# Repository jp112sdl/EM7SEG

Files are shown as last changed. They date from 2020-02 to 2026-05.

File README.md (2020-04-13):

# EM7SEG
electro-mechanical 7 segment display (from dresser/wayne display)
<br/>
_example: use 4 of that nice vintage modules as a clock with a wemos d1 mini, that is getting its time from an ntp service through wifi_

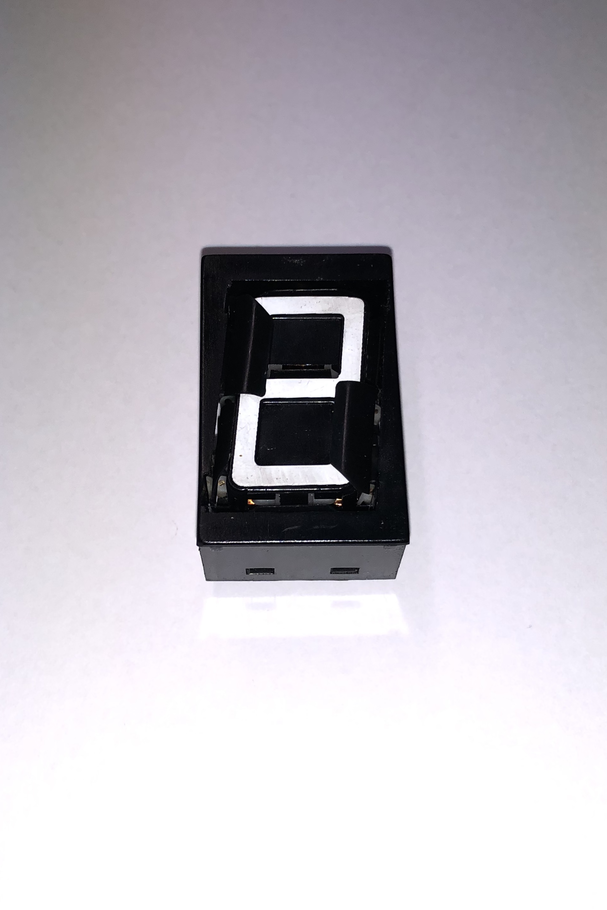
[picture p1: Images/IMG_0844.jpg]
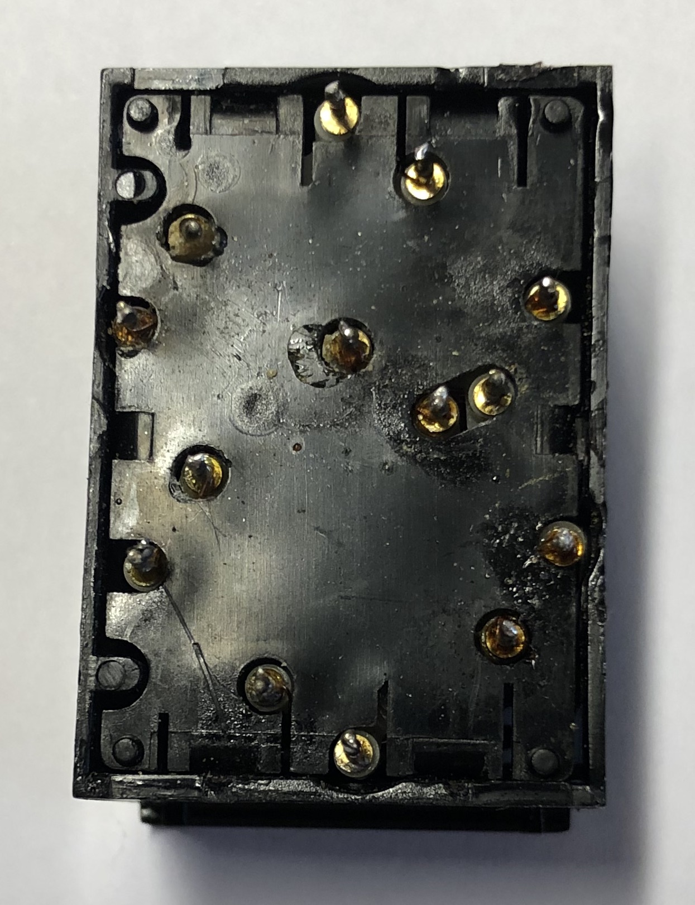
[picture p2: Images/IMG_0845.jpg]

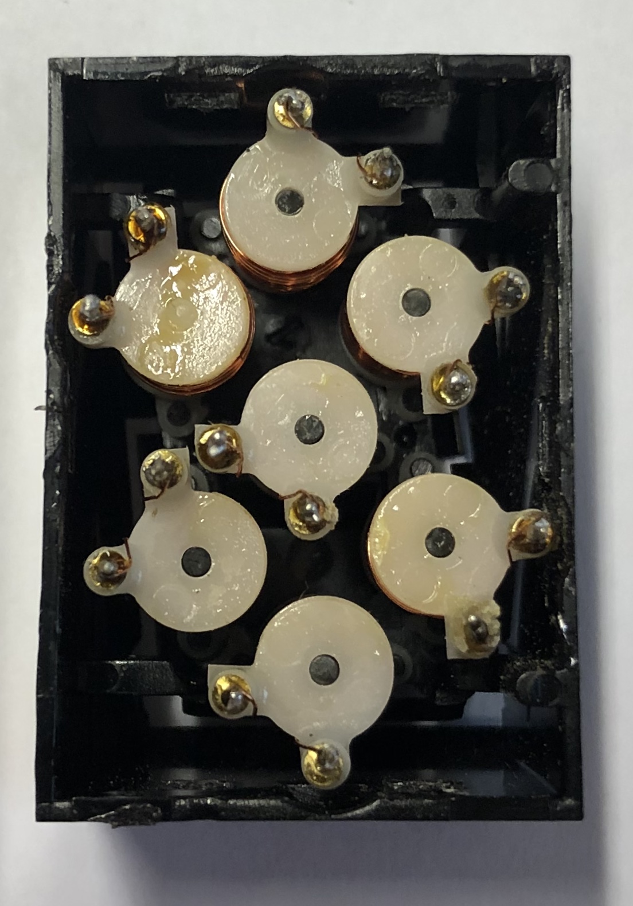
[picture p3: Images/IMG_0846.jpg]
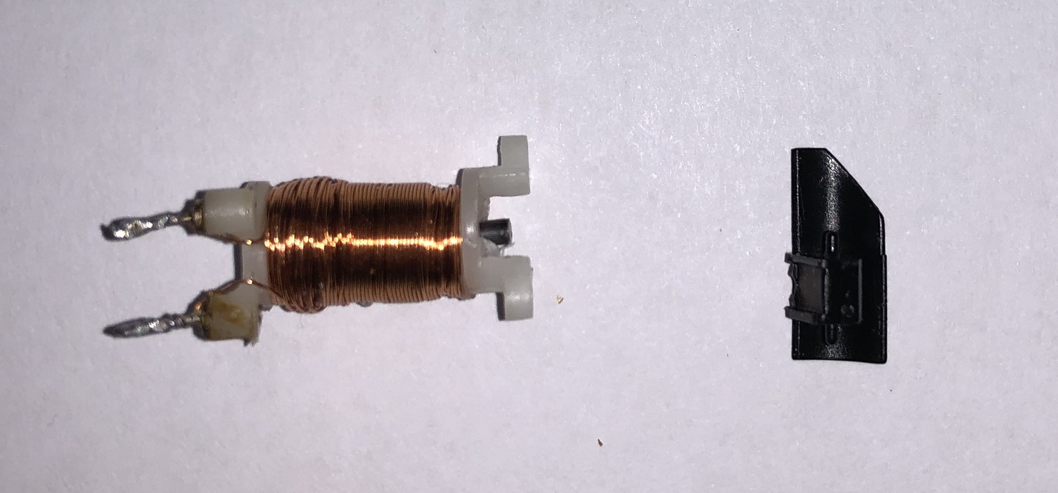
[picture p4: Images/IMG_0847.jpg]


**Teile**
| Ref | Wert | Package | JLCPCB Part |
|---|---|---|---|
| C1, C2 | 100n | 0805 | C49678 |
| R1-R4,R8-R21 | 10k | 0805 | C17414 |
| R5, R6 | 330 | 0805 | C17630 |
| R7 | 1k | 0805 | C17513 |
| D1, D2 | LED green | 0805 | C2297 |
| D3 | LED red | 0805 | C72038 |
| U2 | MCP23017-E/SS | SSOP | - |
| U3 - U9 | L9110S | TSSOP-8 | - |
| J1, J2 | Pin Header 5x | RM 2.0mm | - |

**Pin Header Zuordnung**
| Pin | Beschreibung |
|---|---|
| 1 | GND |
| 2 | Vcc Logik +3.3V / 5V|
| 3 | SDA |
| 4 | SCL |
| 5 | Vcc Segmentspulen 7.5-9V |

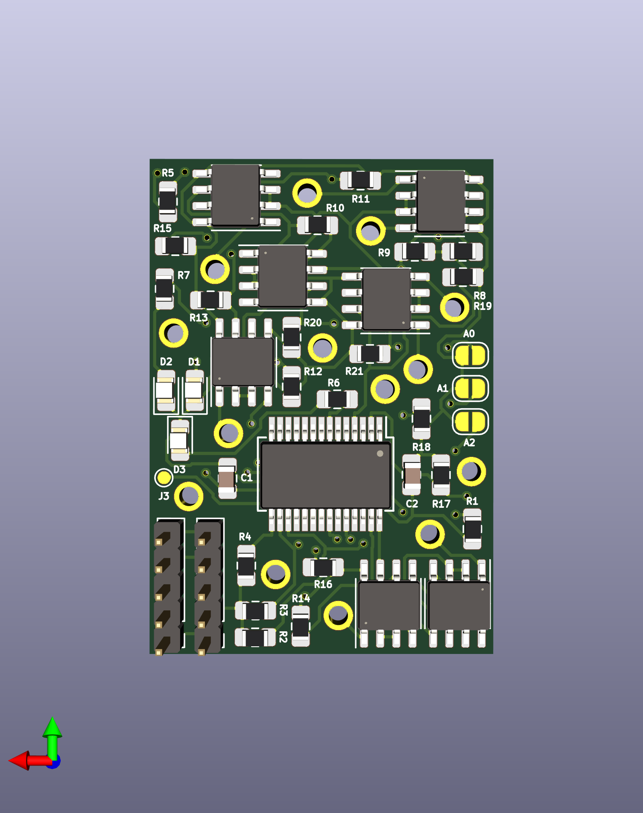
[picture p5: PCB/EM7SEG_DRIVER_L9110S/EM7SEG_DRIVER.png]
driver_pcb


## UPDATE 05.03.2020
### Die Platinen sind angekommen 😍
#### ... und ich habe vergessen, einen Motortreiber (U3) bestücken zu lassen 😤 _(aber gut, das ist kein Problem, den MCP23017 muss ich ohnehin noch selbst auflöten)_
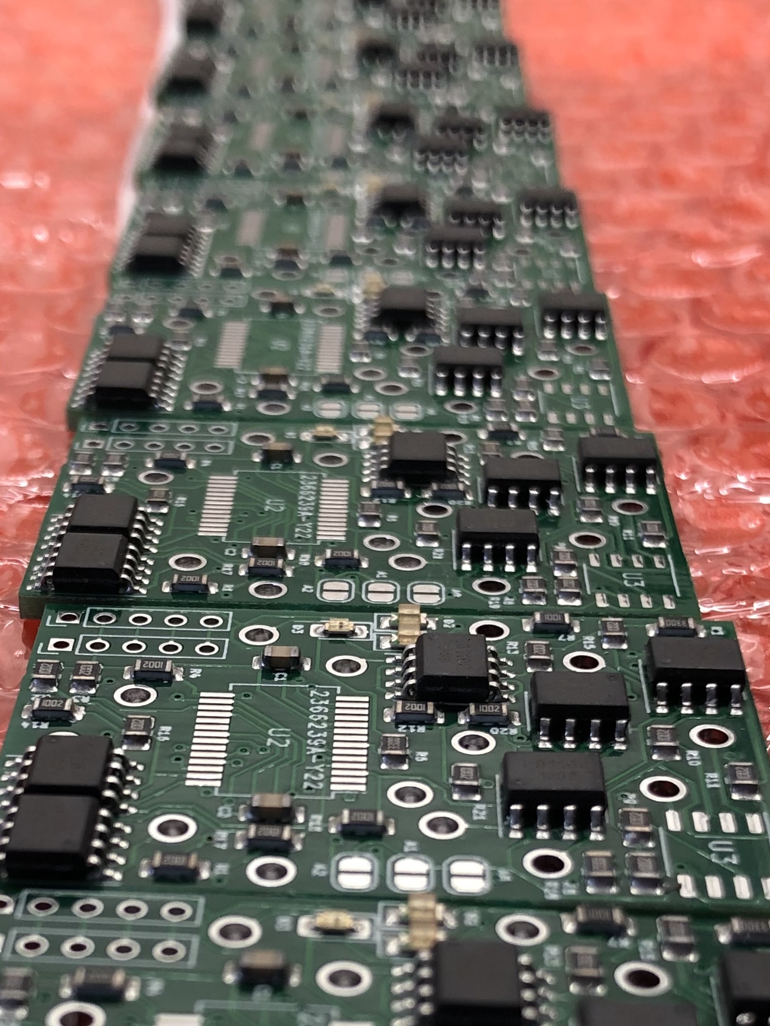
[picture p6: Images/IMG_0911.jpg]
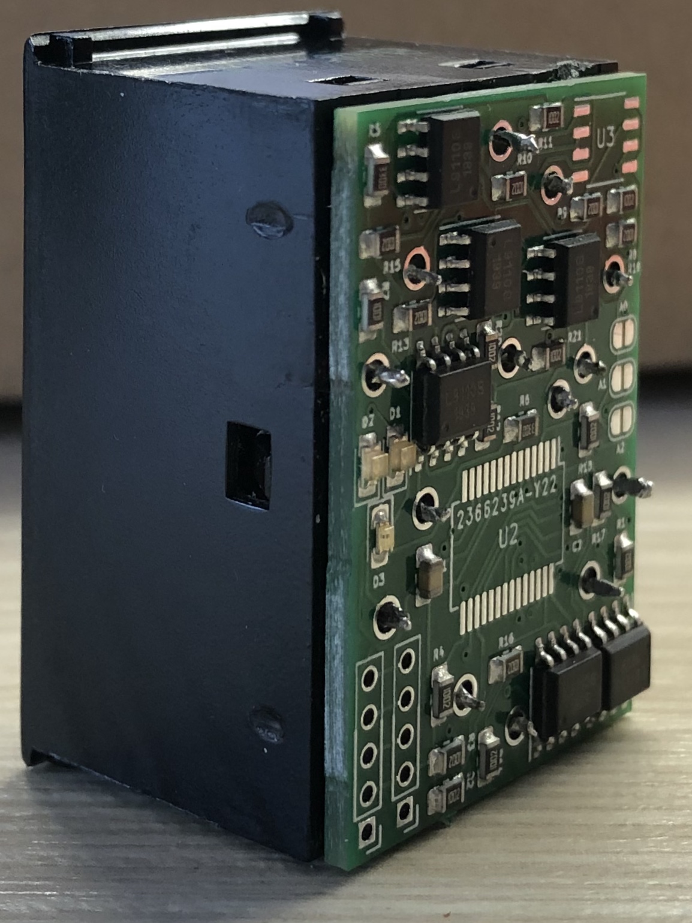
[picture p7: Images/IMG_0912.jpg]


## UPDATE 10.04.2020
### Nach einem kleinen Redesign, sind am 09.04.2020 die Platinen V2.0 gekommen,
#### ...die einen Tag später "verarbeitet wurden"
#### Am schwierigsten war der MCP23017 (SSOP) aufzulöten. Von Hand! 
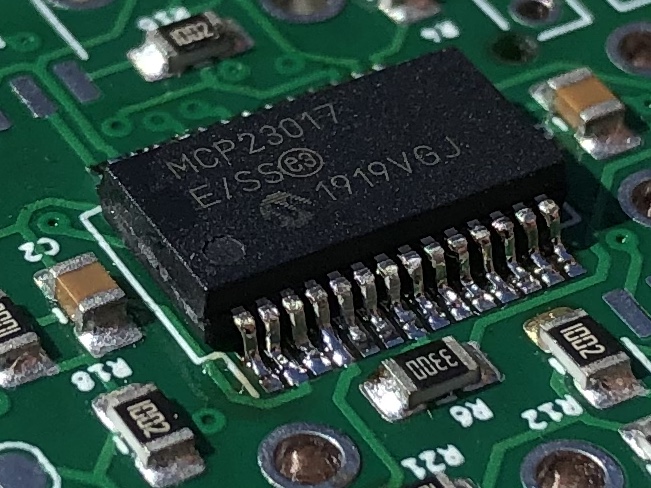
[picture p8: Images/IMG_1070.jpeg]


**Ein Mal angefangen, wurden gleich alle Platinen aufgebaut**</br>
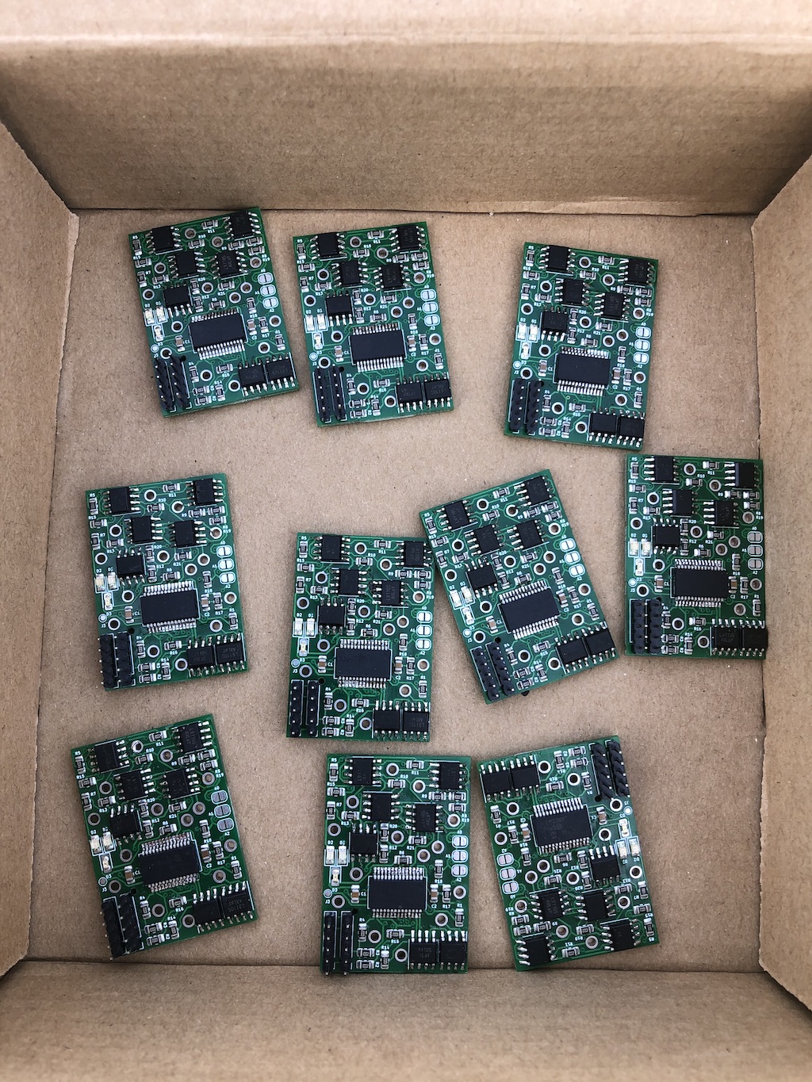
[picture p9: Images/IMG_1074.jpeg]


**und mit den Displaymodulen "verheiratet"**</br>
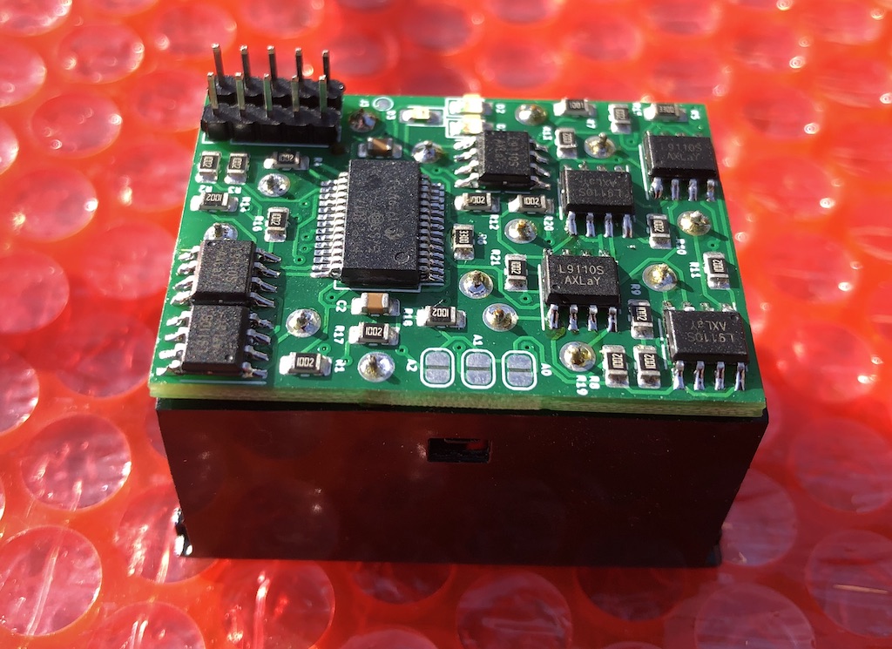
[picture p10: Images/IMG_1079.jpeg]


## UPDATE 11.04.2020
# Die Uhr läuft!
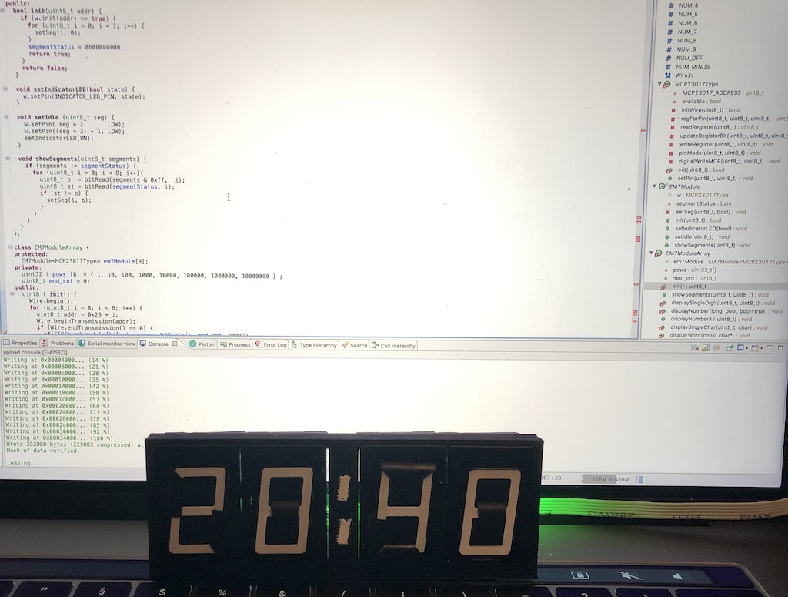
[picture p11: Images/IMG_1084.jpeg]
<br/>
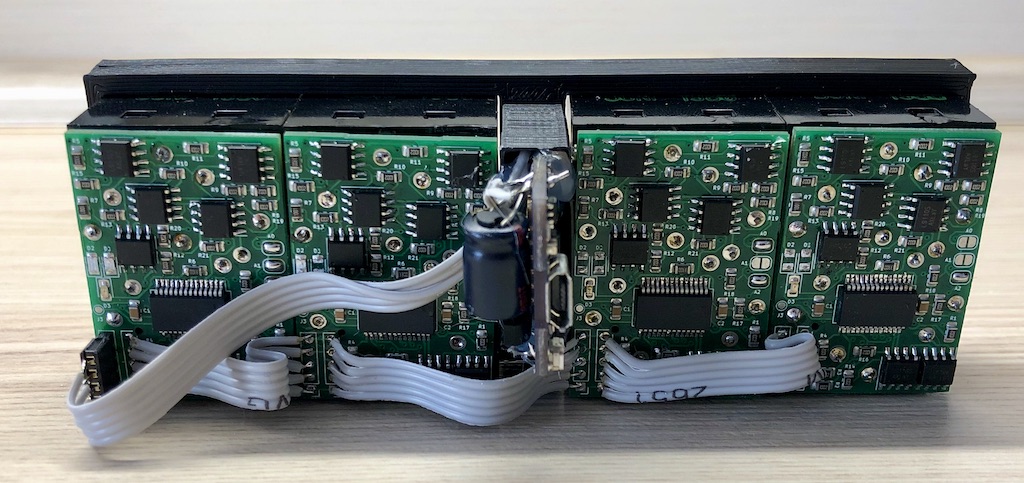
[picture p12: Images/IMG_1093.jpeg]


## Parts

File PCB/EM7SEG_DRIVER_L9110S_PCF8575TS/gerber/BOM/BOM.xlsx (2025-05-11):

Comment | Designator | Footprint | LCSC Part #（optional）
100nF | C1, C2 | 0805_C | C49678
10k | R1, R2, R3, R4,R8, R9, R10, R11, R12, R13, R14, R15, R16, R17, R18, R19, R20, R21 | 0805_R | C17414
330 | R5, R6 | 0805_R | C17630
1k | R7 | 0805_R | C17513
PCF8575TS | U2 | SSOP-24
L9110S | U3, U4, U5, U6, U7, U8, U9 | TSSOP-8
LED | D1, D2 | 0805 | C2297
LED | D3 | 0805 | C72038

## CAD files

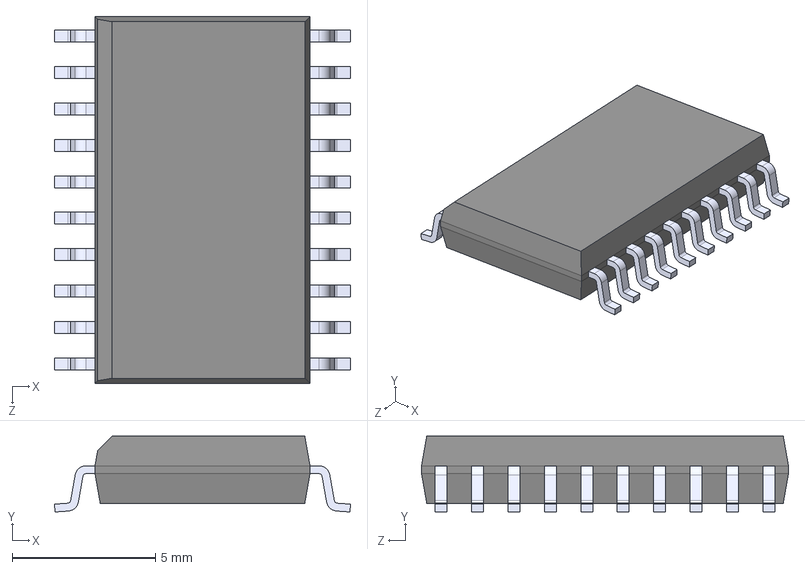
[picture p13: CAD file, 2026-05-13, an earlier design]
PCB/FP7SEG_DRIVER_DRV8848_PCF8575TS Kopie/additional/L293DD.step
10.3 x 2.65 x 12.8 mm

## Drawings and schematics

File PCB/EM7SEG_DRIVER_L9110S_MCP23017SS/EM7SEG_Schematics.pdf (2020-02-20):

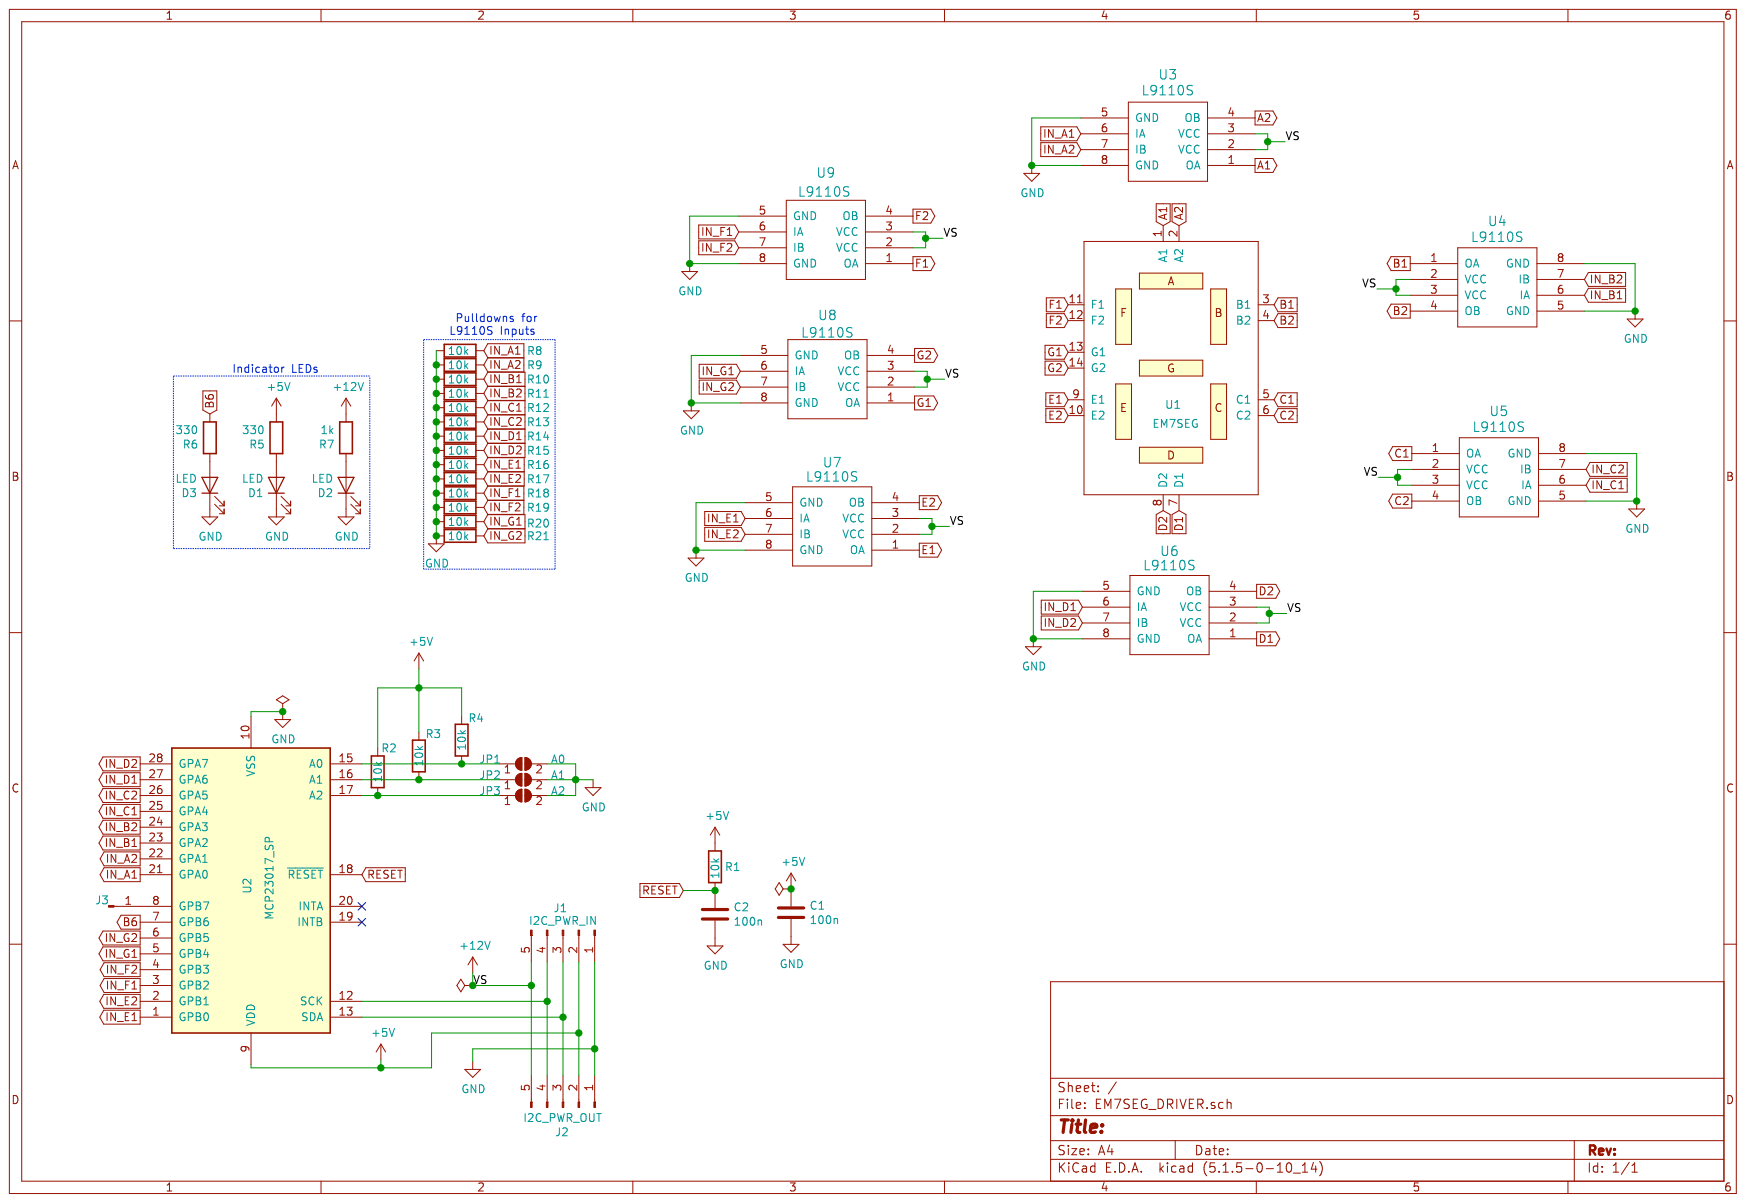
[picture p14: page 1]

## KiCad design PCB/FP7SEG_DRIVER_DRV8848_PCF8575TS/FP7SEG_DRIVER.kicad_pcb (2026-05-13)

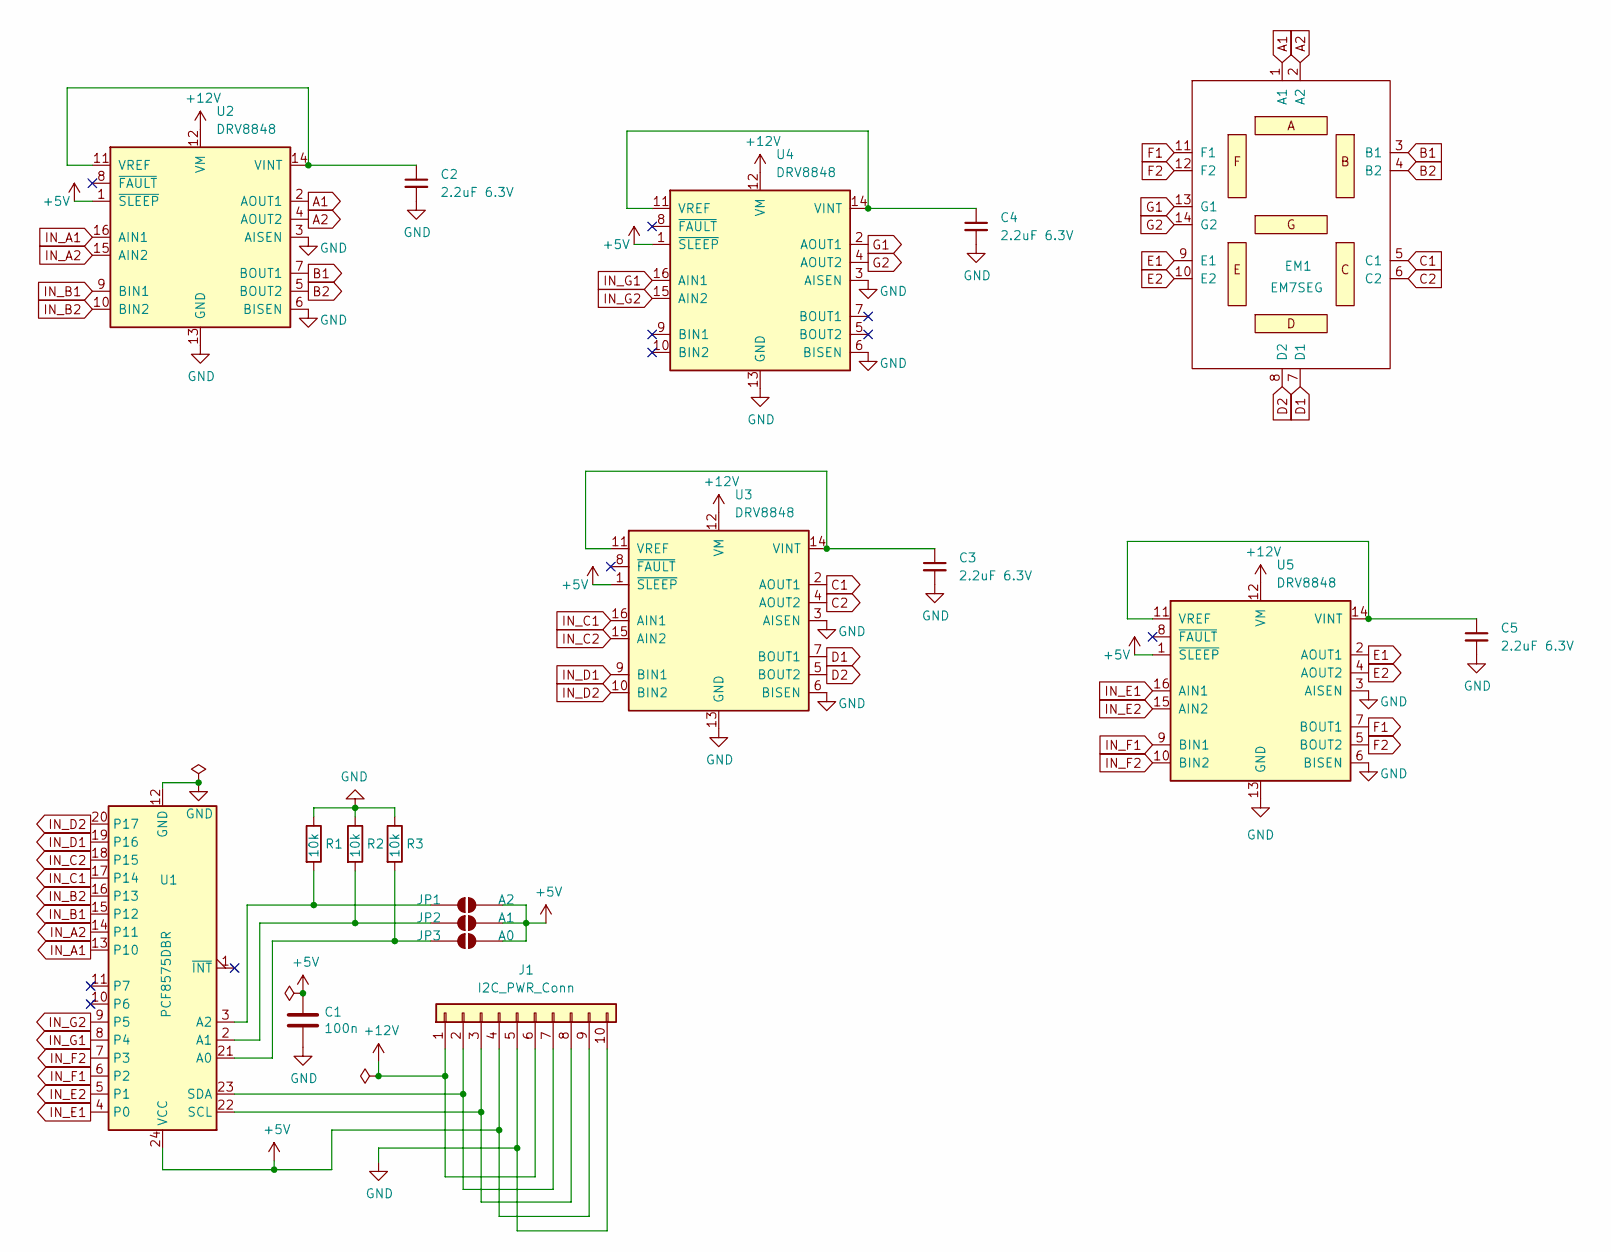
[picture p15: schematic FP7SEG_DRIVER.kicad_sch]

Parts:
C1: 100n; C_0805_2012Metric
C2, C3, C4, C5: 2.2uF 6.3V; C_0805_2012Metric
EM1: EM7SEG; FP
J1: I2C_PWR_Conn; PinSocket_1x10_P2.54mm_Vertical
JP1: A2; SolderJumper-2_P1.3mm_Open_RoundedPad1.0x1.5mm
JP2: A1; SolderJumper-2_P1.3mm_Open_RoundedPad1.0x1.5mm
JP3: A0; SolderJumper-2_P1.3mm_Open_RoundedPad1.0x1.5mm
R1, R2, R3: 10k; R_0805_2012Metric
U1: PCF8575DBR; SSOP-24_5.3x8.2mm_P0.65mm
U2, U3, U4, U5: DRV8848; TSSOP-16-1EP_4.4x5mm_P0.65mm

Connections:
+5V: C1.1, J1.4, J1.9, JP1.2 (B), JP2.2 (B), JP3.2 (B), U1.24 (VCC), U2.1 (~SLEEP), U3.1 (~SLEEP), U4.1 (~SLEEP), U5.1 (~SLEEP)
+12V: J1.1, J1.6, U2.12 (VM), U3.12 (VM), U4.12 (VM), U5.12 (VM)
A1: EM1.1 (A1), U2.2 (AOUT1)
A2: EM1.2 (A2), U2.4 (AOUT2)
B1: EM1.3 (B1), U2.7 (BOUT1)
B2: EM1.4 (B2), U2.5 (BOUT2)
C1: EM1.5 (C1), U3.2 (AOUT1)
C2: EM1.6 (C2), U3.4 (AOUT2)
D1: EM1.7 (D1), U3.7 (BOUT1)
D2: EM1.8 (D2), U3.5 (BOUT2)
E1: EM1.9 (E1), U5.2 (AOUT1)
E2: EM1.10 (E2), U5.4 (AOUT2)
F1: EM1.11 (F1), U5.7 (BOUT1)
F2: EM1.12 (F2), U5.5 (BOUT2)
G1: EM1.13 (G1), U4.2 (AOUT1)
G2: EM1.14 (G2), U4.4 (AOUT2)
GND: C1.2, C2.2, C3.2, C4.2, C5.2, J1.5, J1.10, R1.1, R2.1, R3.1, U1.12 (GND), U2.3 (AISEN), U2.6 (BISEN), U2.13 (GND), U2.17 (GND), U3.3 (AISEN), U3.6 (BISEN), U3.13 (GND), U3.17 (GND), U4.3 (AISEN), U4.6 (BISEN), U4.13 (GND), U4.17 (GND), U5.3 (AISEN), U5.6 (BISEN), U5.13 (GND), U5.17 (GND)
IN_A1: U1.13 (P10), U2.16 (AIN1)
IN_A2: U1.14 (P11), U2.15 (AIN2)
IN_B1: U1.15 (P12), U2.9 (BIN1)
IN_B2: U1.16 (P13), U2.10 (BIN2)
IN_C1: U1.17 (P14), U3.16 (AIN1)
IN_C2: U1.18 (P15), U3.15 (AIN2)
IN_D1: U1.19 (P16), U3.9 (BIN1)
IN_D2: U1.20 (P17), U3.10 (BIN2)
IN_E1: U1.4 (P0), U5.16 (AIN1)
IN_E2: U1.5 (P1), U5.15 (AIN2)
IN_F1: U1.6 (P2), U5.9 (BIN1)
IN_F2: U1.7 (P3), U5.10 (BIN2)
IN_G1: U1.8 (P4), U4.16 (AIN1)
IN_G2: U1.9 (P5), U4.15 (AIN2)
unnamed: J1.2, J1.7, U1.23 (SDA)
unnamed: J1.3, J1.8, U1.22 (SCL)
unnamed: JP1.1 (A), R1.2, U1.3 (A2)
unnamed: JP2.1 (A), R2.2, U1.2 (A1)
unnamed: JP3.1 (A), R3.2, U1.21 (A0)
unnamed: C2.1, U2.11 (VREF), U2.14 (VINT)
unnamed: C3.1, U3.11 (VREF), U3.14 (VINT)
unnamed: C4.1, U4.11 (VREF), U4.14 (VINT)
unnamed: C5.1, U5.11 (VREF), U5.14 (VINT)

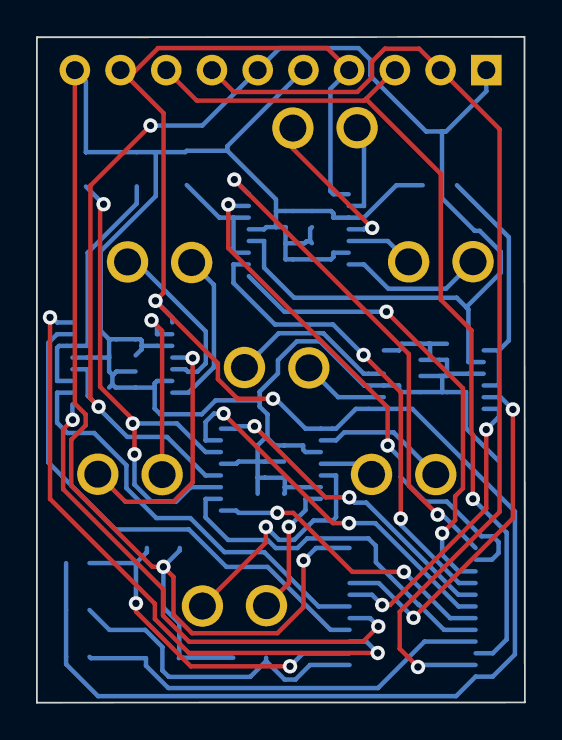
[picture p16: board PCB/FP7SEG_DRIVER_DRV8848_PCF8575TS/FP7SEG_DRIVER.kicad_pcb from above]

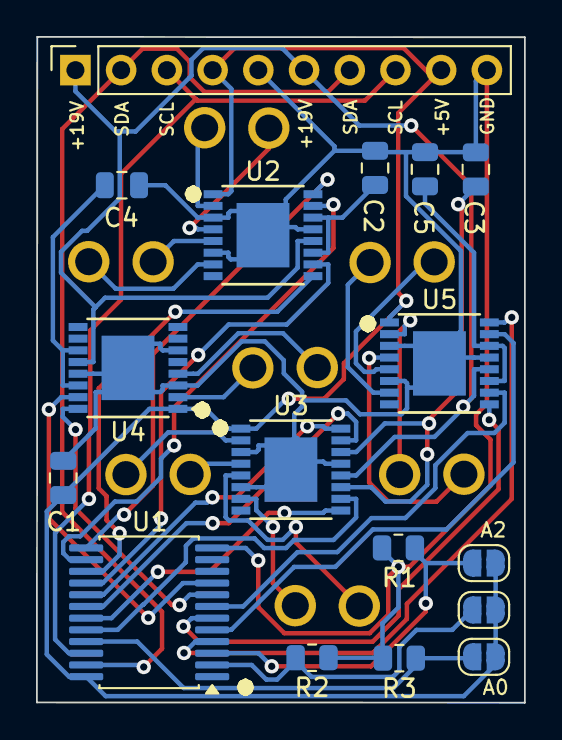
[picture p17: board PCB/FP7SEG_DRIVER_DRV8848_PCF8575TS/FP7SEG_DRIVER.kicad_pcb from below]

Board: 2 copper layers, 27.1 x 37.0 mm, 18 parts (17 on the bottom side), 40 nets.

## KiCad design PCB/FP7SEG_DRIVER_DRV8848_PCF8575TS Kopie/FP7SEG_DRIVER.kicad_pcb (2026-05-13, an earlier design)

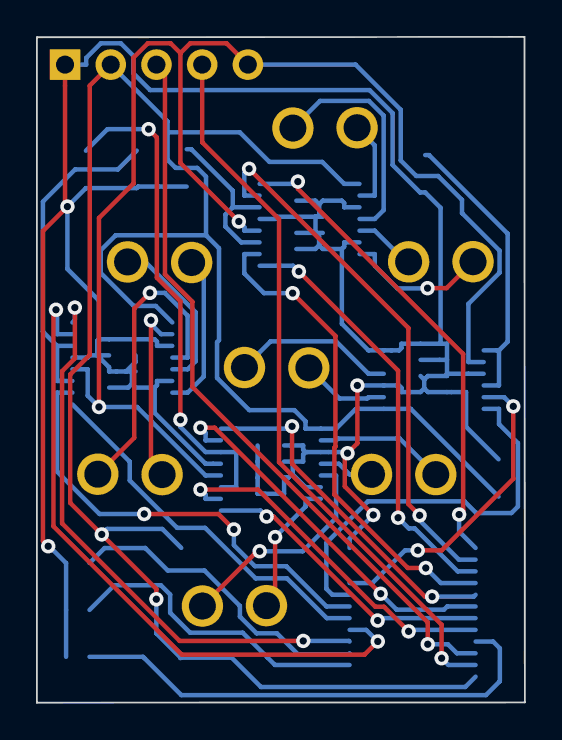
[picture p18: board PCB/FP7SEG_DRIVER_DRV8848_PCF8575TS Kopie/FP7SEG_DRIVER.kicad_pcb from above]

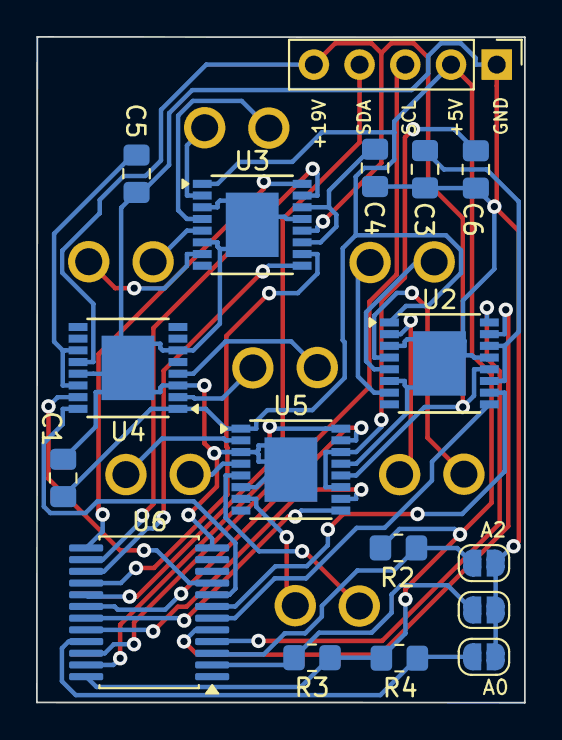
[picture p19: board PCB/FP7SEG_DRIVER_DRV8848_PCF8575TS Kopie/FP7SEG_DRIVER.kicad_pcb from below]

Board: 2 copper layers, 27.1 x 37.0 mm, 18 parts (17 on the bottom side), 40 nets.

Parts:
C1: 100n; C_0805_2012Metric_Pad1.18x1.45mm_HandSolder
C3, C4, C5, C6: 2.2uF 6.3V; C_0805_2012Metric_Pad1.18x1.45mm_HandSolder
EM1: EM7SEG; FP
J1: I2C_PWR_IN; PinHeader_1x05_P2.54mm_Vertical
JP1: A0; SolderJumper-2_P1.3mm_Open_RoundedPad1.0x1.5mm
JP2: A1; SolderJumper-2_P1.3mm_Open_RoundedPad1.0x1.5mm
JP3: A2; SolderJumper-2_P1.3mm_Open_RoundedPad1.0x1.5mm
R2, R3, R4: 10k; R_0805_2012Metric_Pad1.20x1.40mm_HandSolder
U2, U3, U4, U5: DRV8848; TSSOP-16-1EP_4.4x5mm_P0.65mm
U6: PCF8575DBR; SSOP-24_5.3x8.2mm_P0.65mm

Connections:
+5V: C1.1, J1.2, R2.1, R3.1, R4.1, U2.1 (~SLEEP), U3.1 (~SLEEP), U4.1 (~SLEEP), U5.1 (~SLEEP), U6.24 (VCC)
+12V: J1.5, U2.12 (VM), U3.12 (VM), U4.12 (VM), U5.12 (VM)
A1: EM1.1 (A1), U3.2 (AOUT1)
A2: EM1.2 (A2), U3.4 (AOUT2)
B1: EM1.3 (B1), U3.7 (BOUT1)
B2: EM1.4 (B2), U3.5 (BOUT2)
C1: EM1.5 (C1), U5.2 (AOUT1)
C2: EM1.6 (C2), U5.4 (AOUT2)
D1: EM1.7 (D1), U5.7 (BOUT1)
D2: EM1.8 (D2), U5.5 (BOUT2)
E1: EM1.9 (E1), U2.2 (AOUT1)
E2: EM1.10 (E2), U2.4 (AOUT2)
F1: EM1.11 (F1), U2.7 (BOUT1)
F2: EM1.12 (F2), U2.5 (BOUT2)
G1: EM1.13 (G1), U4.2 (AOUT1)
G2: EM1.14 (G2), U4.4 (AOUT2)
GND: C1.2, C3.2, C4.2, C5.2, C6.2, J1.1, JP1.2 (B), JP2.2 (B), JP3.2 (B), U2.3 (AISEN), U2.6 (BISEN), U2.13 (GND), U2.17 (GND), U3.3 (AISEN), U3.6 (BISEN), U3.13 (GND), U3.17 (GND), U4.3 (AISEN), U4.6 (BISEN), U4.13 (GND), U4.17 (GND), U5.3 (AISEN), U5.6 (BISEN), U5.13 (GND), U5.17 (GND), U6.12 (GND)
IN_A1: U3.16 (AIN1), U6.13 (P10)
IN_A2: U3.15 (AIN2), U6.14 (P11)
IN_B1: U3.9 (BIN1), U6.15 (P12)
IN_B2: U3.10 (BIN2), U6.16 (P13)
IN_C1: U5.16 (AIN1), U6.17 (P14)
IN_C2: U5.15 (AIN2), U6.18 (P15)
IN_D1: U5.9 (BIN1), U6.19 (P16)
IN_D2: U5.10 (BIN2), U6.20 (P17)
IN_E1: U2.16 (AIN1), U6.4 (P0)
IN_E2: U2.15 (AIN2), U6.5 (P1)
IN_F1: U2.9 (BIN1), U6.6 (P2)
IN_F2: U2.10 (BIN2), U6.7 (P3)
IN_G1: U4.16 (AIN1), U6.8 (P4)
IN_G2: U4.15 (AIN2), U6.9 (P5)
unnamed: J1.3, U6.22 (SCL)
unnamed: J1.4, U6.23 (SDA)
unnamed: JP1.1 (A), R4.2, U6.21 (A0)
unnamed: JP2.1 (A), R3.2, U6.2 (A1)
unnamed: JP3.1 (A), R2.2, U6.3 (A2)
unnamed: C3.1, U2.11 (VREF), U2.14 (VINT)
unnamed: C4.1, U3.11 (VREF), U3.14 (VINT)
unnamed: C5.1, U4.11 (VREF), U4.14 (VINT)
unnamed: C6.1, U5.11 (VREF), U5.14 (VINT)

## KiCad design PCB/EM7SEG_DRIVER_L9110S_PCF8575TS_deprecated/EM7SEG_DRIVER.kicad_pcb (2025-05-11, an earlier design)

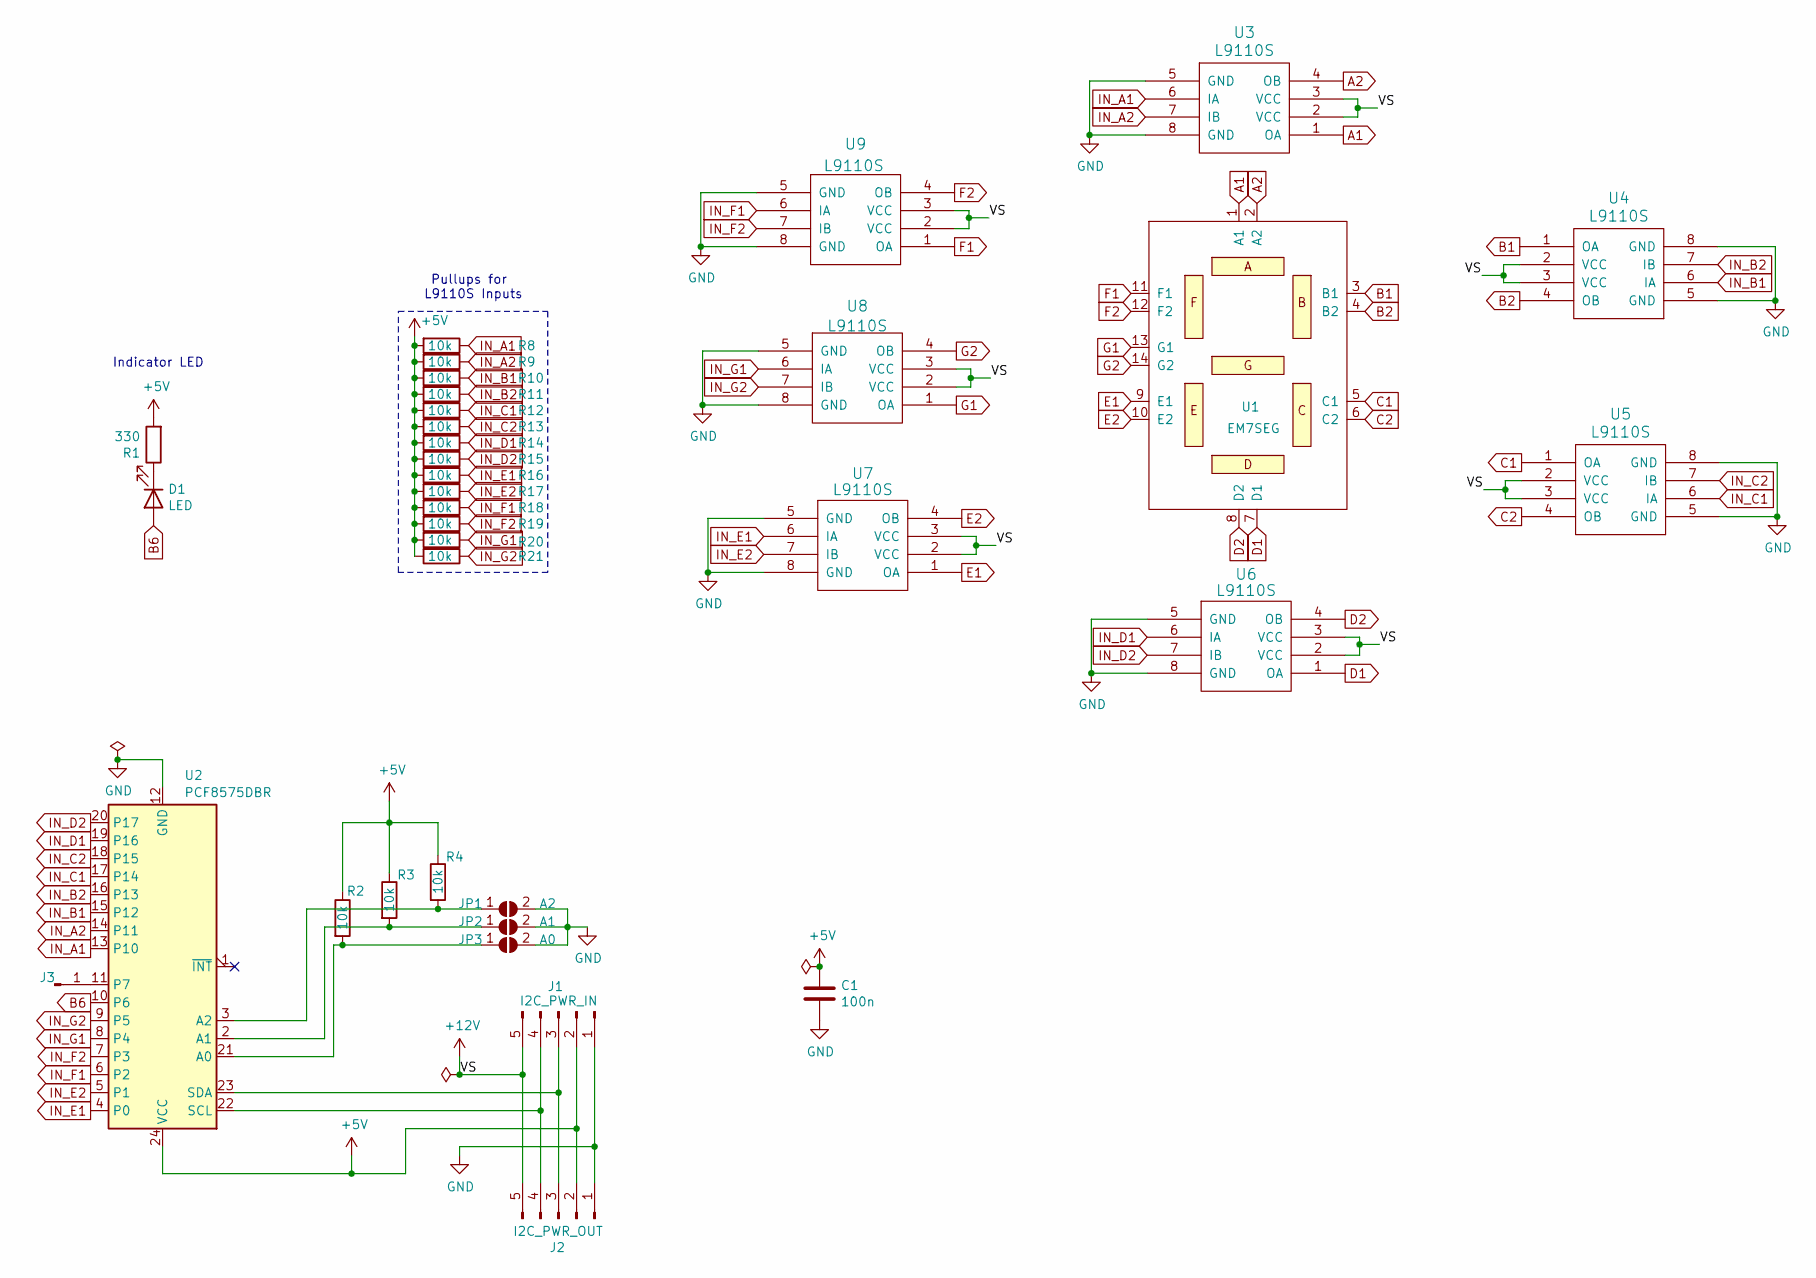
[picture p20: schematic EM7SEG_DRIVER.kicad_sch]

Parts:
C1: 100n; C_0805_2012Metric_Pad1.15x1.40mm_HandSolder
D1: LED; LED_0805_2012Metric_Pad1.15x1.40mm_HandSolder
J1: I2C_PWR_IN; PinHeader_1x05_P2.00mm_Vertical
J2: I2C_PWR_OUT; PinHeader_1x05_P2.00mm_Vertical
J3: Pad_IO16; TestPoint_Pad_D1.0mm
JP1: A0; SolderJumper-2_P1.3mm_Open_RoundedPad1.0x1.5mm
JP2: A1; SolderJumper-2_P1.3mm_Open_RoundedPad1.0x1.5mm
JP3: A2; SolderJumper-2_P1.3mm_Open_RoundedPad1.0x1.5mm
R1: 330; R_0805_2012Metric_Pad1.15x1.40mm_HandSolder
R2, R3, R4, R8, R9, R10, R11, R12, R13, R14, R15, R16, R17, R18, R19, R20, R21: 10k; R_0805_2012Metric_Pad1.15x1.40mm_HandSolder
U1: EM7SEG; em7seg
U2: PCF8575DBR; SSOP-24_5.3x8.2mm_P0.65mm
U3, U4, U5, U6, U7, U8, U9: L9110S; SOP-8_3.9x4.9mm_P1.27mm

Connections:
+5V: C1.1, J1.2, J2.2, R1.2, R2.1, R3.1, R4.1, R8.2, R9.2, R10.2, R11.2, R12.2, R13.2, R14.2, R15.2, R16.2, R17.2, R18.2, R19.2, R20.2, R21.2, U2.24 (VCC)
+12V: J1.5, J2.5, U3.2 (VCC), U3.3 (VCC), U4.2 (VCC), U4.3 (VCC), U5.2 (VCC), U5.3 (VCC), U6.2 (VCC), U6.3 (VCC), U7.2 (VCC), U7.3 (VCC), U8.2 (VCC), U8.3 (VCC), U9.2 (VCC), U9.3 (VCC)
A1: U1.1 (A1), U3.1 (OA)
A2: U1.2 (A2), U3.4 (OB)
B1: U1.3 (B1), U4.1 (OA)
B2: U1.4 (B2), U4.4 (OB)
B6: D1.2 (A), U2.10 (P6)
C1: U1.5 (C1), U5.1 (OA)
C2: U1.6 (C2), U5.4 (OB)
D1: U1.7 (D1), U6.1 (OA)
D2: U1.8 (D2), U6.4 (OB)
E1: U1.9 (E1), U7.1 (OA)
E2: U1.10 (E2), U7.4 (OB)
F1: U1.11 (F1), U9.1 (OA)
F2: U1.12 (F2), U9.4 (OB)
G1: U1.13 (G1), U8.1 (OA)
G2: U1.14 (G2), U8.4 (OB)
GND: C1.2, J1.1, J2.1, JP1.2 (B), JP2.2 (B), JP3.2 (B), U2.12 (GND), U3.5 (GND), U3.8 (GND), U4.5 (GND), U4.8 (GND), U5.5 (GND), U5.8 (GND), U6.5 (GND), U6.8 (GND), U7.5 (GND), U7.8 (GND), U8.5 (GND), U8.8 (GND), U9.5 (GND), U9.8 (GND)
IN_A1: R8.1, U2.13 (P10), U3.6 (IA)
IN_A2: R9.1, U2.14 (P11), U3.7 (IB)
IN_B1: R10.1, U2.15 (P12), U4.6 (IA)
IN_B2: R11.1, U2.16 (P13), U4.7 (IB)
IN_C1: R12.1, U2.17 (P14), U5.6 (IA)
IN_C2: R13.1, U2.18 (P15), U5.7 (IB)
IN_D1: R14.1, U2.19 (P16), U6.6 (IA)
IN_D2: R15.1, U2.20 (P17), U6.7 (IB)
IN_E1: R16.1, U2.4 (P0), U7.6 (IA)
IN_E2: R17.1, U2.5 (P1), U7.7 (IB)
IN_F1: R18.1, U2.6 (P2), U9.6 (IA)
IN_F2: R19.1, U2.7 (P3), U9.7 (IB)
IN_G1: R20.1, U2.8 (P4), U8.6 (IA)
IN_G2: R21.1, U2.9 (P5), U8.7 (IB)
unnamed: D1.1 (K), R1.1
unnamed: J1.3, J2.3, U2.23 (SDA)
unnamed: J1.4, J2.4, U2.22 (SCL)
unnamed: J3.1, U2.11 (P7)
unnamed: JP1.1 (A), R4.2, U2.3 (A2)
unnamed: JP2.1 (A), R3.2, U2.2 (A1)
unnamed: JP3.1 (A), R2.2, U2.21 (A0)

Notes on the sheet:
Pullups for L9110S Inputs
Indicator LED

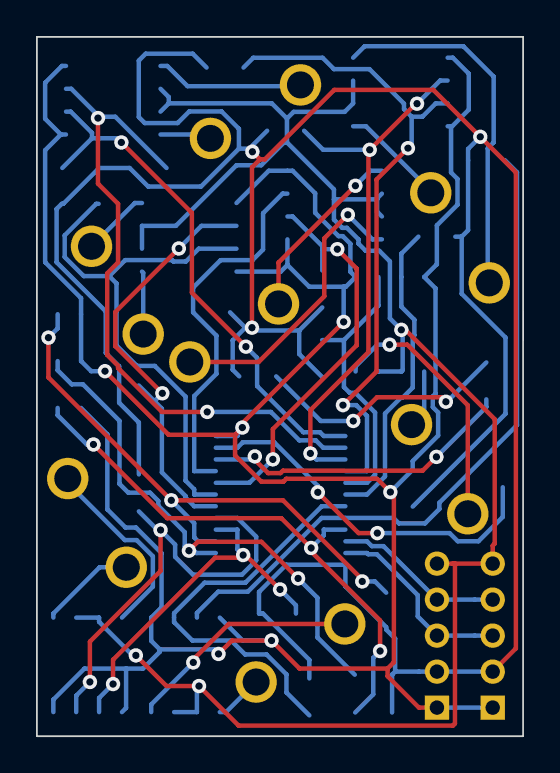
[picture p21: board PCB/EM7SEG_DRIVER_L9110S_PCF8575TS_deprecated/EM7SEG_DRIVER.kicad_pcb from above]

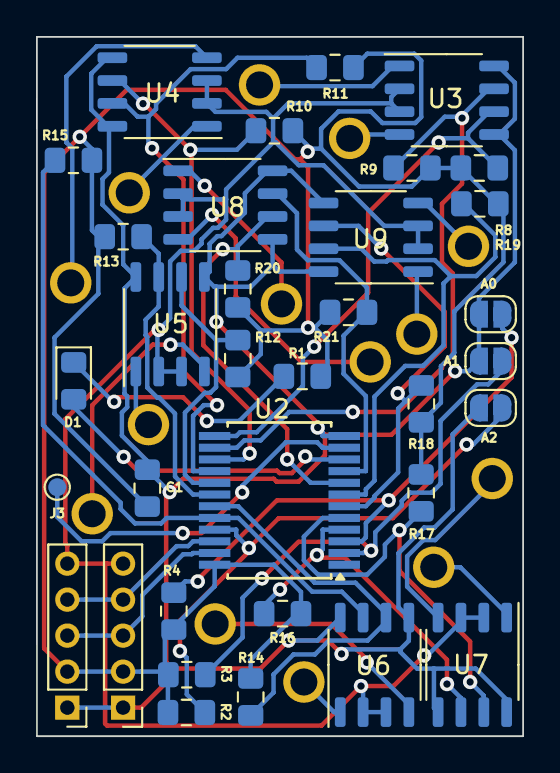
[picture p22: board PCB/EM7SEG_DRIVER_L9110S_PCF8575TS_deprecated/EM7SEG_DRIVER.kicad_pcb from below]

Board: 2 copper layers, 27.0 x 38.8 mm, 35 parts (34 on the bottom side), 39 nets.

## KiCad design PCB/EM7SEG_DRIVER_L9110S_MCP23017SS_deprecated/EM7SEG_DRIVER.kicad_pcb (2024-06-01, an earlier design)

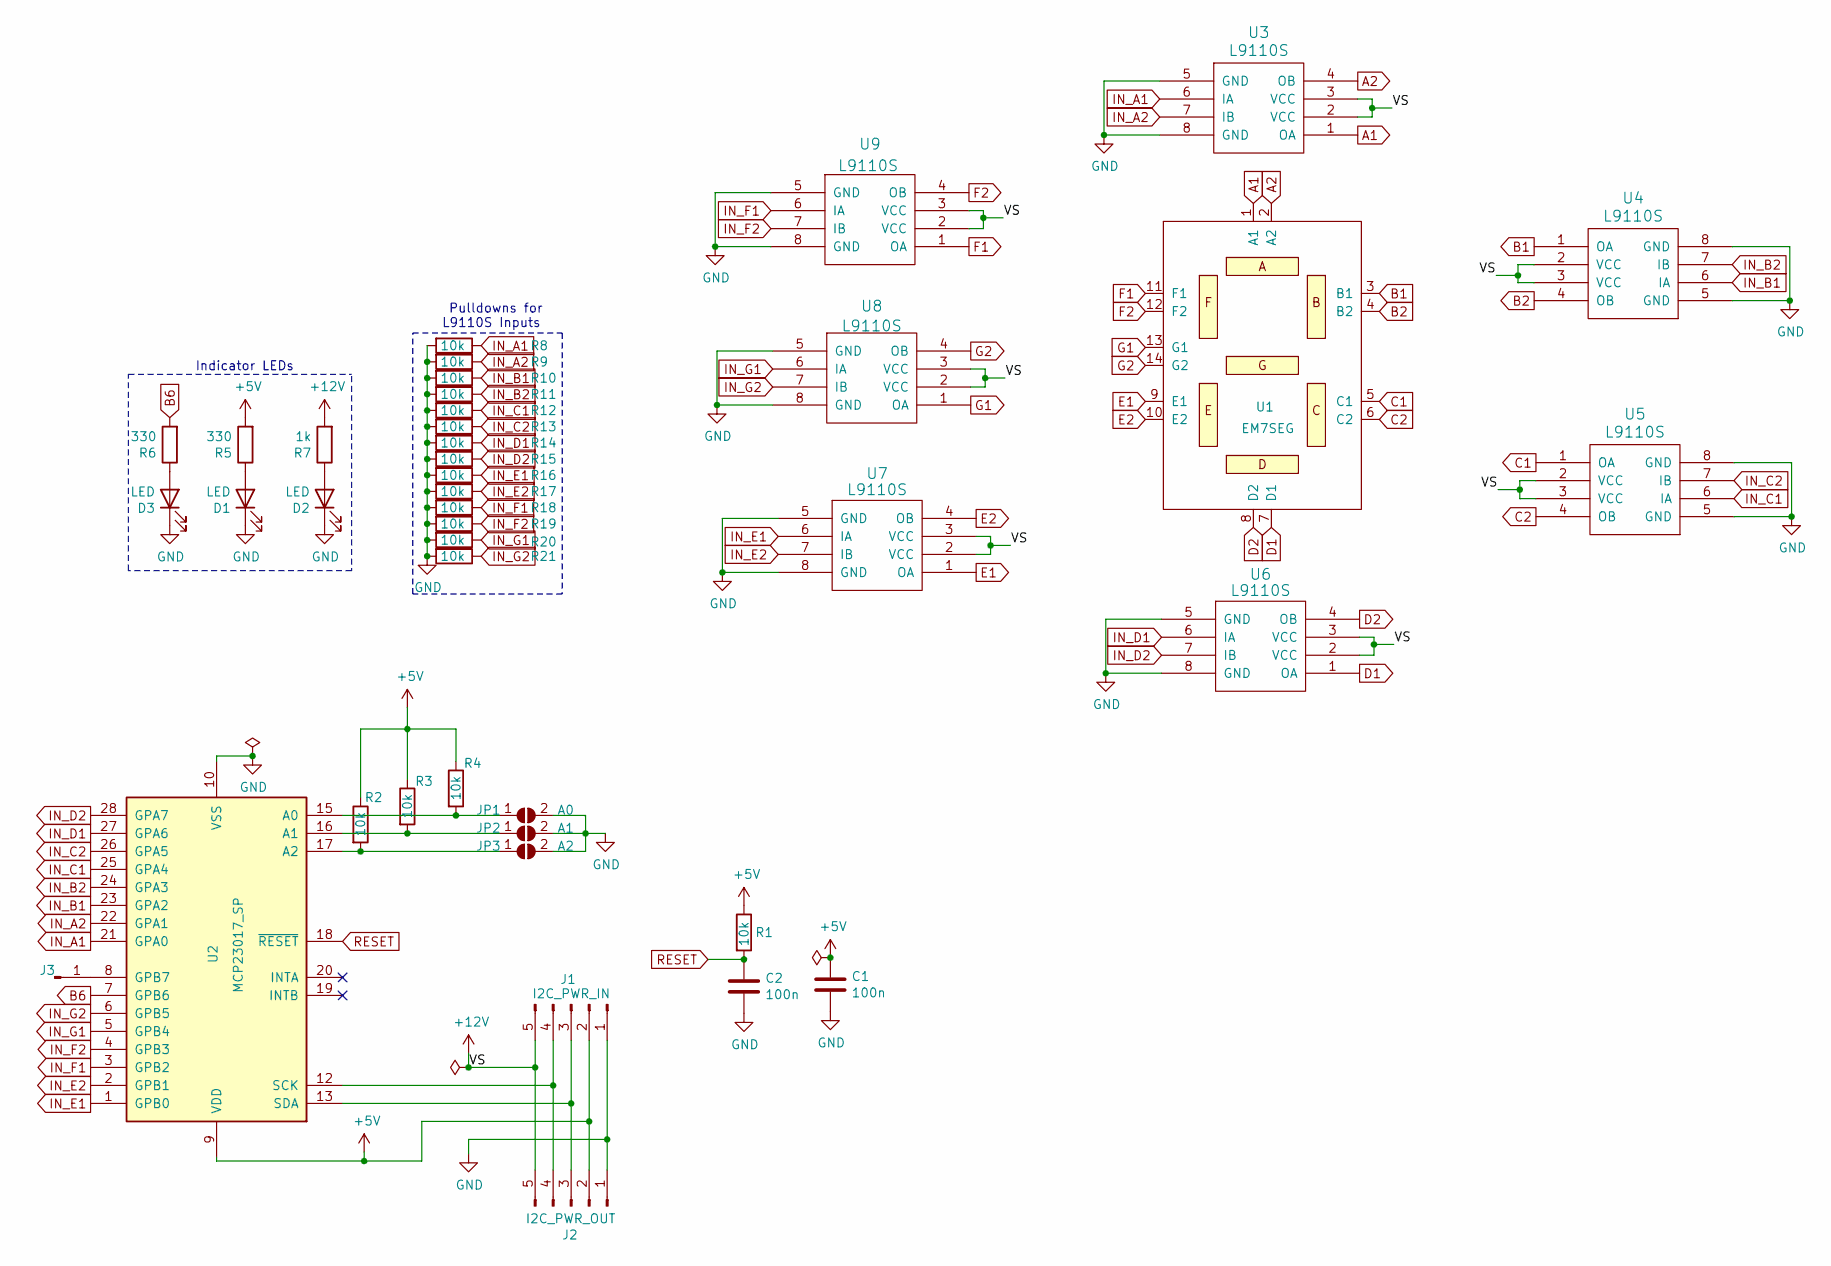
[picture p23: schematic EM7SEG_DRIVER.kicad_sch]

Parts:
C1, C2: 100n; C_0805_2012Metric_Pad1.15x1.40mm_HandSolder
D1, D2, D3: LED; LED_0805_2012Metric_Pad1.15x1.40mm_HandSolder
J1: I2C_PWR_IN; PinHeader_1x05_P2.00mm_Vertical
J2: I2C_PWR_OUT; PinHeader_1x05_P2.00mm_Vertical
J3: Pad_IO16; TestPoint_Pad_D1.0mm
JP1: A0; SolderJumper-2_P1.3mm_Open_RoundedPad1.0x1.5mm
JP2: A1; SolderJumper-2_P1.3mm_Open_RoundedPad1.0x1.5mm
JP3: A2; SolderJumper-2_P1.3mm_Open_RoundedPad1.0x1.5mm
R1, R2, R3, R4, R8, R9, R10, R11, R12, R13, R14, R15, R16, R17, R18, R19, R20, R21: 10k; R_0805_2012Metric_Pad1.15x1.40mm_HandSolder
R5, R6: 330; R_0805_2012Metric_Pad1.15x1.40mm_HandSolder
R7: 1k; R_0805_2012Metric_Pad1.15x1.40mm_HandSolder
U1: EM7SEG; em7seg
U2: MCP23017_SP; SSOP-28_5.3x10.2mm_P0.65mm
U3, U4, U5, U6, U7, U8, U9: L9110S; SOP-8_3.9x4.9mm_P1.27mm

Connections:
+5V: C1.1, J1.2, J2.2, R1.1, R2.1, R3.1, R4.1, R5.2, U2.9 (VDD)
+12V: J1.5, J2.5, R7.2, U3.2 (VCC), U3.3 (VCC), U4.2 (VCC), U4.3 (VCC), U5.2 (VCC), U5.3 (VCC), U6.2 (VCC), U6.3 (VCC), U7.2 (VCC), U7.3 (VCC), U8.2 (VCC), U8.3 (VCC), U9.2 (VCC), U9.3 (VCC)
A1: U1.1 (A1), U3.1 (OA)
A2: U1.2 (A2), U3.4 (OB)
B1: U1.3 (B1), U4.1 (OA)
B2: U1.4 (B2), U4.4 (OB)
B6: R6.2, U2.7 (GPB6)
C1: U1.5 (C1), U5.1 (OA)
C2: U1.6 (C2), U5.4 (OB)
D1: U1.7 (D1), U6.1 (OA)
D2: U1.8 (D2), U6.4 (OB)
E1: U1.9 (E1), U7.1 (OA)
E2: U1.10 (E2), U7.4 (OB)
F1: U1.11 (F1), U9.1 (OA)
F2: U1.12 (F2), U9.4 (OB)
G1: U1.13 (G1), U8.1 (OA)
G2: U1.14 (G2), U8.4 (OB)
GND: C1.2, C2.2, D1.1 (K), D2.1 (K), D3.1 (K), J1.1, J2.1, JP1.2 (B), JP2.2 (B), JP3.2 (B), R8.2, R9.2, R10.2, R11.2, R12.2, R13.2, R14.2, R15.2, R16.2, R17.2, R18.2, R19.2, R20.2, R21.2, U2.10 (VSS), U3.5 (GND), U3.8 (GND), U4.5 (GND), U4.8 (GND), U5.5 (GND), U5.8 (GND), U6.5 (GND), U6.8 (GND), U7.5 (GND), U7.8 (GND), U8.5 (GND), U8.8 (GND), U9.5 (GND), U9.8 (GND)
IN_A1: R8.1, U2.21 (GPA0), U3.6 (IA)
IN_A2: R9.1, U2.22 (GPA1), U3.7 (IB)
IN_B1: R10.1, U2.23 (GPA2), U4.6 (IA)
IN_B2: R11.1, U2.24 (GPA3), U4.7 (IB)
IN_C1: R12.1, U2.25 (GPA4), U5.6 (IA)
IN_C2: R13.1, U2.26 (GPA5), U5.7 (IB)
IN_D1: R14.1, U2.27 (GPA6), U6.6 (IA)
IN_D2: R15.1, U2.28 (GPA7), U6.7 (IB)
IN_E1: R16.1, U2.1 (GPB0), U7.6 (IA)
IN_E2: R17.1, U2.2 (GPB1), U7.7 (IB)
IN_F1: R18.1, U2.3 (GPB2), U9.6 (IA)
IN_F2: R19.1, U2.4 (GPB3), U9.7 (IB)
IN_G1: R20.1, U2.5 (GPB4), U8.6 (IA)
IN_G2: R21.1, U2.6 (GPB5), U8.7 (IB)
unnamed: D1.2 (A), R5.1
unnamed: D2.2 (A), R7.1
unnamed: D3.2 (A), R6.1
unnamed: J1.3, J2.3, U2.13 (SDA)
unnamed: J1.4, J2.4, U2.12 (SCK)
unnamed: J3.1, U2.8 (GPB7)
unnamed: JP1.1 (A), R4.2, U2.15 (A0)
unnamed: JP2.1 (A), R3.2, U2.16 (A1)
unnamed: JP3.1 (A), R2.2, U2.17 (A2)
RESET: C2.1, R1.2, U2.18 (~RESET)

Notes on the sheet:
Pulldowns for L9110S Inputs
Indicator LEDs

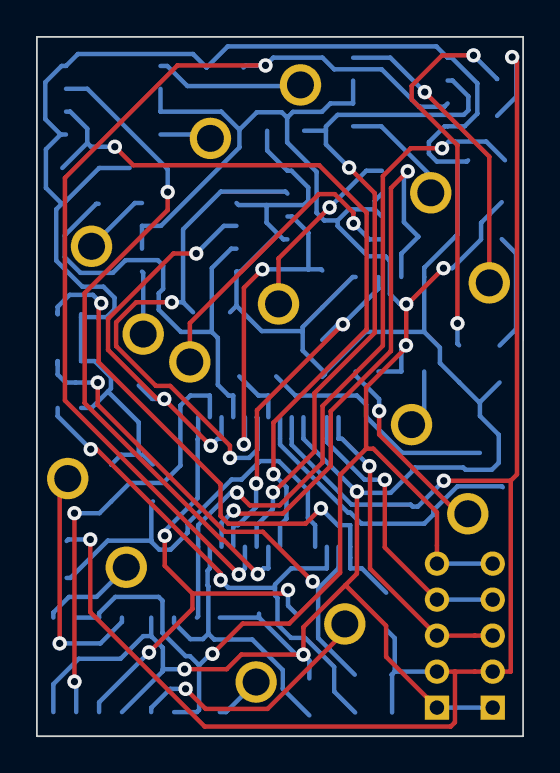
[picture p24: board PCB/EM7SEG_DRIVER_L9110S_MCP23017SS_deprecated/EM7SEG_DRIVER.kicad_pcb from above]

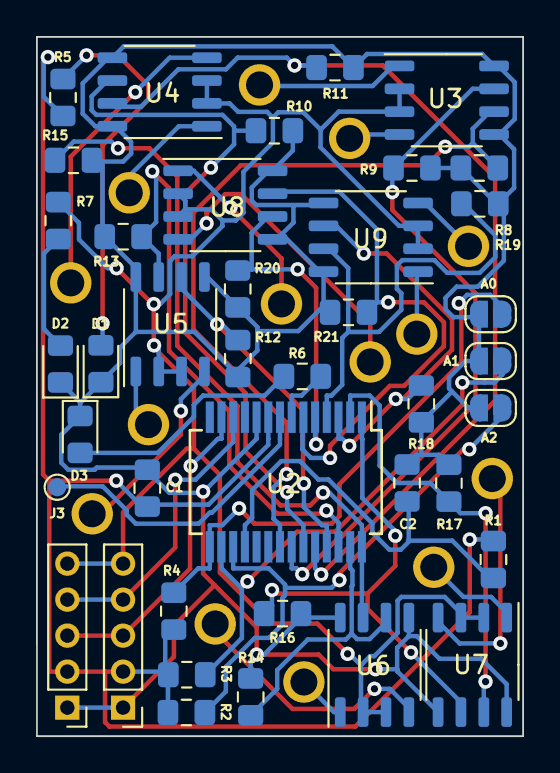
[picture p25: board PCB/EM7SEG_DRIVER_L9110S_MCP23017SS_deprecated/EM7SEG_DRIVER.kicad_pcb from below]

Board: 2 copper layers, 27.0 x 38.8 mm, 41 parts (40 on the bottom side), 42 nets.

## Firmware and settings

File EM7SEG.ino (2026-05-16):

#define LOGLEVEL 0

#include <ArduinoOTA.h>
#include <ESP8266mDNS.h>
#include <ESP8266HTTPUpdateServer.h>
#include <ESP8266WebServer.h>


#include "printf_helper.h"
#include "Em7seg_cntrl.h"
EM7ModuleArray<MCP23017Type, 4> d;

#include "WiFiFunctions.h"
#include "NtpFunctions.h"

#define ENABLE_PIN D7

      uint8_t lastMinute = 0;
      uint8_t lastHour   = 0;
const uint16_t segDly    = 60;
const char * host = "em7segclock";


ESP8266WebServer server(80);
ESP8266HTTPUpdateServer httpUpdater;

void startOTAhandling() {
  Serial.print(F("Starte OTA-Handler... "));
  ArduinoOTA.onStart([]() {
    Serial.println(F("Start updating"));
  });
  ArduinoOTA.onEnd([]() {
    Serial.print("\nEnd");
  });
  ArduinoOTA.onProgress([](__attribute__ ((unused))unsigned int progress,__attribute__ ((unused)) unsigned int total) {
    Serial.print(".");
  });
  ArduinoOTA.onError([](ota_error_t error) {
    Serial.print("Error "+String(error));
    if (error == OTA_AUTH_ERROR) Serial.print("Auth Failed");
    else if (error == OTA_BEGIN_ERROR) Serial.print("Begin Failed");
    else if (error == OTA_CONNECT_ERROR) Serial.print("Connect Failed");
    else if (error == OTA_RECEIVE_ERROR) Serial.print("Receive Failed");
    else if (error == OTA_END_ERROR) Serial.print("End Failed");
  });

  ArduinoOTA.setHostname(host);
  ArduinoOTA.begin();
  Serial.println("done");
}

void rotateAnimation() {
  d.showSegments(4, 0b00010000);
  d.showSegments(4, 0b00110000);
  d.showSegments(4, 0b00110001);
  d.showSegments(3, 0b00000001);
  d.showSegments(2, 0b00000001);
  d.showSegments(1, 0b00000001);
  d.showSegments(1, 0b00000011);
  d.showSegments(1, 0b00000111);
  d.showSegments(1, 0b00001111);
  d.showSegments(2, 0b00001001);
  d.showSegments(3, 0b00001001);
  d.showSegments(4, 0b00111001);

  d.showSegments(4, 0b00101001);
  d.showSegments(4, 0b00001001);
  d.showSegments(4, 0b00001000);
  d.showSegments(3, 0b00001000);
  d.showSegments(2, 0b00001000);
  d.showSegments(1, 0b00001110);
  d.showSegments(1, 0b00001100);
  d.showSegments(1, 0b00001000);
  d.showSegments(1, 0b00000000);
  d.showSegments(2, 0b00000000);
  d.showSegments(3, 0b00000000);
  d.showSegments(4, 0b00000000);
}

void setup() {
  Serial.begin(57600);
  Serial.println("Start");
  uint8_t moduleCount = d.init(ENABLE_PIN);
  if (moduleCount == 0) {
    delay(1000);
    ESP.restart();
  }

  d.setSegToSegDelayMillis(10);

  doWifiConnect();
  setNTPSettings();

  d.setSegToSegDelayMillis(segDly);

  MDNS.begin(host);

  startOTAhandling();

  httpUpdater.setup(&server);

  server.begin();
}

void showtime(uint8_t h, uint8_t m) {
  uint16_t t = ((h*100)+m);
  p("%01d\n",t);
  d.displayNumber(t, true);
}

void loop() {
  checkSyncEventTriggered();
  ArduinoOTA.handle();
  server.handleClient();

  uint8_t h = hour();
  uint8_t m = minute();

  //do a nice rotation animation every hour
  if (lastHour != h) {
    lastHour = h;

    d.clear();

    d.setSegToSegDelayMillis(segDly / 2);
    for (uint8_t i = 0; i < 2; i++) {
      rotateAnimation();
    }
    d.setSegToSegDelayMillis(segDly);

    delay(300);

    showtime(h, m);

    lastMinute = m;
  }
  //if minute changes, refresh display
  else if (lastMinute != m) {
    lastMinute = m;
    showtime(h, m);
  }

  delay(0);
}

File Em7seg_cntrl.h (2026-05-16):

//- -----------------------------------------------------------------------------------------------------------------------
// Em7seg_cntrl
// 2020-02-16 jp112sdl Creative Commons - http://creativecommons.org/licenses/by-nc-sa/3.0/de/
//- -----------------------------------------------------------------------------------------------------------------------

#ifndef EM7SEG_CNTRL_H_
#define EM7SEG_CNTRL_H_

//um -1 in einem einzelnen Segment anzuzeigen (z.B. bei Thermometern)
//#define MINUS10_CONDENSED

#include "printf_helper.h"

#define MCP23017_IODIRA 0x00
#define MCP23017_IODIRB 0x01
#define MCP23017_GPIOA  0x12
#define MCP23017_GPIOB  0x13
#define MCP23017_OLATA  0x14
#define MCP23017_OLATB  0x15

#define ON  1
#define OFF 0

//                           GFEDCBA
#define NUM_SEGMENTS_0    0b00111111  //        SegA:0
#define NUM_SEGMENTS_1    0b00000110  //       --------
#define NUM_SEGMENTS_2    0b01011011  //      |        |
#define NUM_SEGMENTS_3    0b01001111  //SegF:5|        |SegB:1
#define NUM_SEGMENTS_4    0b01100110  //      | SegG:6 |
#define NUM_SEGMENTS_5    0b01101101  //       --------
#define NUM_SEGMENTS_6    0b01111101  //      |        |
#define NUM_SEGMENTS_7    0b00000111  //SegE:4|        |SegC:2
#define NUM_SEGMENTS_8    0b01111111  //      |        |
#define NUM_SEGMENTS_9    0b01101111  //       --------
#define NUM_SEGMENTS_OFF  0b00000000  //        SegD:3
#define NUM_SEGMENTS_MIN  0b01000000  //
#define NUM_SEGMENTS_MIN1 0b01000110  //

#define CHR_SEGMENTS_MIN { 45,  NUM_SEGMENTS_MIN }
#define CHR_SEGMENTS_0   { 48,  NUM_SEGMENTS_0 }
#define CHR_SEGMENTS_1   { 49,  NUM_SEGMENTS_1 }
#define CHR_SEGMENTS_2   { 50,  NUM_SEGMENTS_2 }
#define CHR_SEGMENTS_3   { 51,  NUM_SEGMENTS_3 }
#define CHR_SEGMENTS_4   { 52,  NUM_SEGMENTS_4 }
#define CHR_SEGMENTS_5   { 53,  NUM_SEGMENTS_5 }
#define CHR_SEGMENTS_6   { 54,  NUM_SEGMENTS_6 }
#define CHR_SEGMENTS_7   { 55,  NUM_SEGMENTS_7 }
#define CHR_SEGMENTS_8   { 56,  NUM_SEGMENTS_8 }
#define CHR_SEGMENTS_9   { 57,  NUM_SEGMENTS_9 }
#define CHR_SEGMENTS_A   { 65,  0b01110111 }
#define CHR_SEGMENTS_C   { 67,  0b00111001 }
#define CHR_SEGMENTS_E   { 69,  0b01111001 }
#define CHR_SEGMENTS_F   { 70,  0b01110001 }
#define CHR_SEGMENTS_H   { 72,  0b01110110 }
#define CHR_SEGMENTS_I   { 73,  NUM_SEGMENTS_1 }
#define CHR_SEGMENTS_L   { 76,  0b00111000 }
#define CHR_SEGMENTS_O   { 79,  NUM_SEGMENTS_0 }
#define CHR_SEGMENTS_P   { 80,  0b01110011 }
#define CHR_SEGMENTS_S   { 83,  NUM_SEGMENTS_5 }
#define CHR_SEGMENTS_U   { 85,  0b00111110 }
#define CHR_SEGMENTS_b   { 98,  0b01111100 }
#define CHR_SEGMENTS_c   { 99,  0b01011000 }
#define CHR_SEGMENTS_d   { 100, 0b01011110 }
#define CHR_SEGMENTS_n   { 110, 0b01010100 }
#define CHR_SEGMENTS_o   { 111, 0b01011100 }
#define CHR_SEGMENTS_r   { 114, 0b01010000 }
#define CHR_SEGMENTS_t   { 116, 0b01111000 }
#define CHR_SEGMENTS_u   { 117, 0b00011100 }


#define SEG_INV          0b11111111  // <- change polarity for single segment

#define NUM_SEGMENTS_ARRAY_LEN   13
const uint8_t Numbers[NUM_SEGMENTS_ARRAY_LEN] = {
    NUM_SEGMENTS_0,
    NUM_SEGMENTS_1,
    NUM_SEGMENTS_2,
    NUM_SEGMENTS_3,
    NUM_SEGMENTS_4,
    NUM_SEGMENTS_5,
    NUM_SEGMENTS_6,
    NUM_SEGMENTS_7,
    NUM_SEGMENTS_8,
    NUM_SEGMENTS_9,
    NUM_SEGMENTS_OFF,
    NUM_SEGMENTS_MIN,
    NUM_SEGMENTS_MIN1
    };

#define CHR_SEGMENTS_ARRAY_LEN 30
const uint8_t Characters[CHR_SEGMENTS_ARRAY_LEN][2] = {
    CHR_SEGMENTS_MIN,
    CHR_SEGMENTS_0,
    CHR_SEGMENTS_1,
    CHR_SEGMENTS_2,
    CHR_SEGMENTS_3,
    CHR_SEGMENTS_4,
    CHR_SEGMENTS_5,
    CHR_SEGMENTS_6,
    CHR_SEGMENTS_7,
    CHR_SEGMENTS_8,
    CHR_SEGMENTS_9,
    CHR_SEGMENTS_A,
    CHR_SEGMENTS_C,
    CHR_SEGMENTS_E,
    CHR_SEGMENTS_F,
    CHR_SEGMENTS_H,
    CHR_SEGMENTS_I,
    CHR_SEGMENTS_L,
    CHR_SEGMENTS_O,
    CHR_SEGMENTS_P,
    CHR_SEGMENTS_S,
    CHR_SEGMENTS_U,
    CHR_SEGMENTS_b,
    CHR_SEGMENTS_c,
    CHR_SEGMENTS_d,
    CHR_SEGMENTS_n,
    CHR_SEGMENTS_o,
    CHR_SEGMENTS_r,
    CHR_SEGMENTS_t,
    CHR_SEGMENTS_u
};

#define NUM_0      0
#define NUM_1      1
#define NUM_2      2
#define NUM_3      3
#define NUM_4      4
#define NUM_5      5
#define NUM_6      6
#define NUM_7      7
#define NUM_8      8
#define NUM_9      9
#define NUM_OFF   10
#define NUM_MINUS 11
#define NUM_MINUS1 12

#include <Wire.h>

class PCF8575Type {
private:
  uint8_t  PCF8575_ADDRESS = 0x20;
  bool     INVERT          = false;
  uint16_t dataValue       = 0x0000;
  bool     available       = false;

  bool initWire(uint8_t addr) {
    Wire.beginTransmission(addr);
    return (Wire.endTransmission() == 0);
  }

  void digitalWritePCF(uint8_t pin, bool d) {
    bool val = (INVERT == true) ? !d : d;
    if (val == HIGH) {
      dataValue &= ~(1 << pin);
    } else {
      dataValue |= (1 << pin);
    }
    Wire.beginTransmission(PCF8575_ADDRESS);
    Wire.write(dataValue >> 8);        //  high 8 bits
    Wire.write(dataValue & 0xFF);      //  low 8 bits
    Wire.endTransmission();
  }

public:
  bool init(uint8_t addr, bool inv) {
    PCF8575_ADDRESS = addr;
    INVERT = inv;

    if (initWire(PCF8575_ADDRESS) == true) {
      for (uint8_t i = 0; i < 16; i++){
        digitalWritePCF(i, HIGH);
      }
#if LOGLEVEL > 2
      pf(F("PCF8575Type: init PCF8575 with address %#01x done\n"),addr);
#endif
      available = true;
      return true;
    }
    pf(F("PCF8575Type: no PCF8575 found at address %#01x\n"),addr);
    available = false;
    return false;
  }

  void setPin(uint8_t pin, uint8_t d) {
    if (available) digitalWritePCF(pin, d);
  }
};
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

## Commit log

2020-02-18 update BOM
    [BOM.xlsx]
2020-02-19 update pcb
    [BOM.xlsx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]
2020-02-20 use pull-downs instead of pull-ups for l9110 inputs
    [EM7SEG_DRIVER-B_Cu.gbr, EM7SEG_DRIVER-B_Mask.gbr, EM7SEG_DRIVER-B_Paste.gbr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]
2020-02-20 update gerber
    [EM7SEG_DRIVER-B_Cu.gbr, EM7SEG_DRIVER-B_Mask.gbr, EM7SEG_DRIVER-B_Paste.gbr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]
2020-04-03 fix parts enumeration
    [BOM.xlsx]
2020-04-13 disable indicator led
2020-04-13 switch the modules off/on to strobe a reset
    [Em7seg_cntrl.h]
2020-04-13 add delay between segment switches to make smooth animation
2021-04-09 fixed case
2022-01-12 update kicad
2024-06-01 update kicad version
    [EM7SEG_DRIVER.kicad_pcb, EM7SEG_DRIVER.kicad_sch]
2025-05-11 New PCB for PCF8757 IC
    [BOM.xlsx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]
